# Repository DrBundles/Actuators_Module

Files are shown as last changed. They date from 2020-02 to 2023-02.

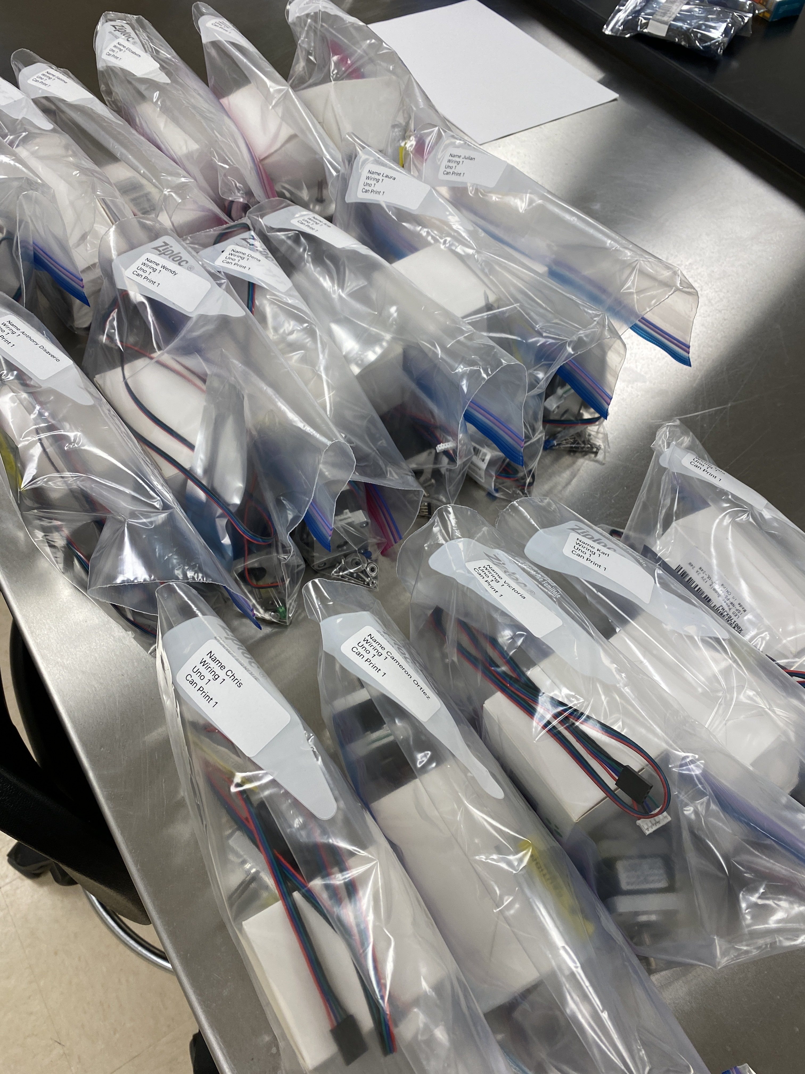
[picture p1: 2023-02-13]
Parts/Parts_Pickup_1.JPG

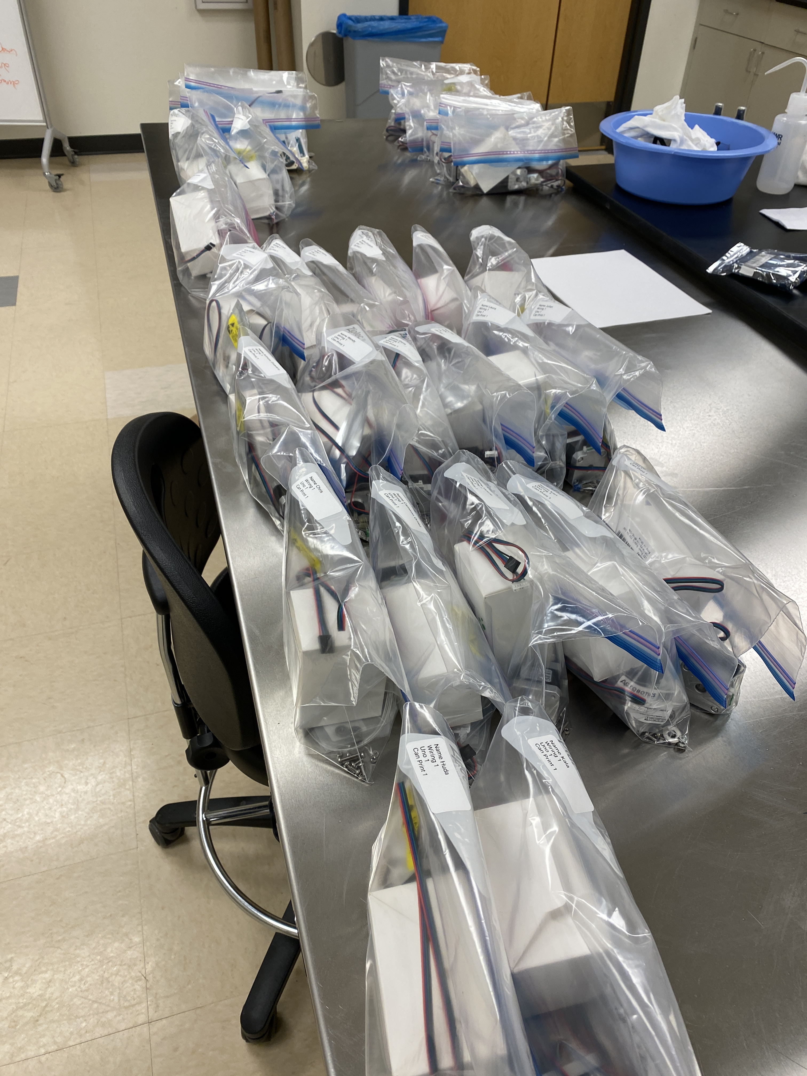
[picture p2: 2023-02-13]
Parts/Parts_Pickup_2.JPG

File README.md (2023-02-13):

# Actuators_Module

# Video Links
- [Materials Part 1](https://ucdenver.hosted.panopto.com/Panopto/Pages/Viewer.aspx?id=055986f1-c3ec-4268-8f4e-aeb30160cd68)
- [Code Day 1 Part 1](https://ucdenver.hosted.panopto.com/Panopto/Pages/Viewer.aspx?id=c7519612-6c13-432e-b2ea-aeb30160e118) 
- [Code Day 1 Part 2](https://ucdenver.hosted.panopto.com/Panopto/Pages/Viewer.aspx?id=c81cfcb9-6042-4e62-9a67-aeb30160f008)
- [Code Day 2 Part 1](https://ucdenver.hosted.panopto.com/Panopto/Pages/Viewer.aspx?id=9c95f3c9-c75f-416a-9927-aeb30160e0f4)
- [Code Day 2 Part 2](https://ucdenver.hosted.panopto.com/Panopto/Pages/Viewer.aspx?id=abec7e0b-8e1e-48be-8ef7-aeb301610b54)
- [Code Day 2 Part 3](https://ucdenver.hosted.panopto.com/Panopto/Pages/Viewer.aspx?id=a6deae2b-6028-43d2-8763-aeb30160e47a)
- [Code Day 3 Part 1](https://ucdenver.hosted.panopto.com/Panopto/Pages/Viewer.aspx?id=0ca2a75e-c111-4d63-9ddc-aeb30160e49d)

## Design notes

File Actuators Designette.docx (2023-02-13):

# Actuators Designette

Lecture Notes:

- Students will be given the User Story and User Needs.
- Design Inputs will be filled in together in-class as a discussion.
- Students will be given one design output and one corresponding verification test.
- Students will generate their own Design Outputs and corresponding verification tests that match up with the given Design Inputs.
- Validation tests will be provided but not completed as part of this experiment.
- Measuring of Rotational Speed will be extra credit if the students develop a method to do this in lab. Otherwise, it will need to be detailed how this would be done in practice within the Design Process documentation.

# User Story

Would you help me to design a new motor to drive my machine? My old motor died and I need to replace it. I have to turn a ¼” shaft at precisely 122RPM for 12.234 seconds. This process must operate in concert with my other equipment so I need it to be electronically controlled. Also, the current machine does not let us know what the actual RPM is. It would be really nice to know what the RPM is so we can track it as part of our QMS. We don’t need to automatically log this information though, we can just read it off of a screen. Thanks for the help!

Torque!

# User Needs

ID | Title | Description
UN-1 | Rotational Output | The user needs to rotate a ¼” shaft.
UN-2 | Rotation RPM | The user needs to rotate a shaft at 122RM
UN-3 | Rotation Controls | The user needs to control the shaft motion automatically, not using a manual switch.
UN-4 | Rotation Duration | The user needs to precisely control the duration of rotation to 12.234 seconds.
UN-5 | Rotation Measuring | The user needs a method to monitor shaft rotational speed for QMS.

## Design Inputs

ID | Link | Title | Description
DI-1 | UN-1 | Connection | The device shall mechanically couple to a ¼ inch input shaft.
DI-2 | UN-1 | Motion | The device shall rotate the input shaft detailed in DI-1.
DI-3 | UN-2 | RPM Speed | The device shall rotate the input shaft detailed in DI-2 at 122 RPM ±1 RPM.
DI-4 | UN-3 | Controls | The device shall be controlled through automatic actuation that interfaces with the existing electronic system.
DI-5 | UN-4 | Duration | The device shall rotate the output shaft detailed in DI-1 at the rate detailed in DI-3 for 12.234 ± .001 seconds.
DI-6 | UN-5 | RPM Measure | The device shall provide a visual indication of the RPM speed detailed in DI-3.

## Design Outputs

ID | Link | Title | Description
DO-1 | DI-1 | Shaft Coupling | The device shall mechanically mate with the user’s ¼” input shaft through a rigid set-screw type coupling.
DO-2 | DI-2 DI-3 | Motor | The device will use a DC brushed gearhead motor coupled to a custom gearbox to achieve the 122 RPM rotational motion.
DO-3 | DI-2 | Housing | The motor and gearbox shall be affixed to a housing.
DO-4 | DI-1 DI-2 | Housing Mount | The motor housing will be affixed to the existing machine frame using the existing threaded mounting holes utilized by the previous motor housing.
DO-5 | DI-2 DI-4 | Motor Power | The device motor shall use the same 12V DC supply as the previous electric motor (3A max load).
DO-6 | DI-4 DI-5 DI-6 | Controls Microcontroller | The device will use an Arduino microcontroller to control motor state (on/off), runtime duration, and RPM measurement and indication.
DO-7 | DI-4 DI-5 | Motor Controls | The electric motor will be switched using a power MOSFET rated for the appropriate load based on the chosen electronic components.
DO-8 | DI-6 | RPM Measurement | The output shaft rotational speed will be measured using a photodiode / laser encoder that is monitored by the Arduino firmware.
DO-9 | DI-6 | RPM Indication | RPM values will be indicated to the user through a USB / serial connection. Values will be shown in the Arduino Serial Plotter running on a computer monitor.

## Verification

ID | Link | Title | Description | Test Protocol
VE-1 | DI-1 | Connection to Shaft | Test that the device mechanically connects to a ¼” shaft in a manner that allows for rotary motion without slippage or misalignment. | PV-1
VE-2 | DI-1 | Mounting | Test that the motor housing bolt pattern matches the bolt pattern dimensions on the existing equipment. | PV-2
VE-3 | DI-2 | Rotation | Test that the gearbox and shaft allow for unrestricted rotational motion by removing the gearhead motor and manually turning the input drive gear. | PV-3
VE-4 | DI-3 | RPM | Test that output shaft rotates at 122 RPM ±1 RPM. | PV-4
VE-5 | DI-4 | Controls | Test that the Arduino can automatically change the motor state (on/off). | PV-5
VE-6 | DI-5 | Duration | Verify that the device drive motor remains energized and in motion for 12.234 ± .001 seconds | PV-6
VE-7 | DI-6 | RPM Measure | Verify that the RPM value as measured by the encoder and Arduino matches the value as measured using the independent technique outlined in VE-4. | PV-7
VE-8 | DI-6 | RPM Indication | Verify that the RPM value measured in VE-7 matches the value indicated within the user interface. | PV-8

## Validation

ID | Link | Title | Description | Test Protocol
VL-1 | UN-1 | Mounting | Test that the motor, gearbox and housing successfully mounts to the existing equipment as detailed in DO-4. | PL-1
VL-2 | UN-1 | Connection to Shaft | Test that the device mechanically connects to the existing ¼” input shaft in a manner that allows for rotary motion without slippage or misalignment. This test shall be conducted with the motor housing mounted to the existing frame. | PL-2
VL-3 | UN-2 | Rotation | Test that the gearbox and shaft allow for unrestricted rotational motion by removing the gearhead motor and manually turning the input drive gear while the housing and input shaft is mounted to existing equipment. | PL-3
VL-4 | UN-2 | Rotation | Test that the energized motor can rotate the input drive shaft of existing equipment. | PL-3
VL-5 | UN-2 | RPM | Test that output shaft rotates at 122 RPM ±1 RPM while connected to existing equipment. | PL-3
VL-6 | UN-3 | Controls | Test that the Arduino can automatically change the motor state (on/off) when controlled by input signal from existing equipment | PL-4
VL-7 | UN-4 | Duration | Test that the device drive motor remains energized and in motion for 12.234 ± .001 seconds while connected to existing equipment. | PL-5
VL-8 | UN-5 | RPM Measure | Test that the RPM value as measured by the encoder and Arduino is displayed and can be read by the user. | PL-6
VL-9 | UN-1 UN-2 UN-3 UN-4 | User Interface | Test that the user can properly use new device when operating existing equipment. | PL-7

## Traceability Matrix

Build a traceability matrix that has some values omitted. Students must fill in the omitted values.

NOTE: Add titles to the Trace matrix below

User Need | Design Input | Design Output | Verification | Validation
UN-1 | DI-1 | DO-1,4 | VE-1 | VL-2
| | | VE-2 | VL-1
| DI-2 | DO-2,3,4,5 | VE-3 | VL-9
UN-2 | DI-3 | DO-2 | VE-4 | VL-3
| | | | VL-4
| | | | VL-9
UN-3 | DI-4 | DO-5,6,7 | VE-5 | VL-6
| | | | VL-9
UN-4 | DI-5 | DO-6,7 | VE-6 | VL-7
| | | | VL-9
UN-5 | DI-6 | DO-6,8,9 | VE-7 | VL-8
| | DO-6,8,9 | VE-8

## Testing Protocols

One sample test protocol, students must generate several more test protocols.

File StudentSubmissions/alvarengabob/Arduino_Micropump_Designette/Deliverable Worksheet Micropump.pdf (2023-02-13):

Intro. to Biodesign
BIOE 3090 | Design Controls Worksheet

## Micropump Module

### Design Controls Worksheet – 50 Pts

## ID: DCW-1

Due Date: 2/13/2020 11:59 PM, Canvas Upload

Date Written – 04/02/2020
Date Revised – 04/04/2020
Author: Alyssa Salazar, Bob Alvarenga, Gage Murray, Luis Rodriguez, Mikala Mueller

## Improvement of Existing Design User Needs

User Needs Matrix
ID | Description
UN-1 | Improved UX / UI to allow for operator control.
UN-2 | Improve Solidworks files to include assembly, hardware, configurations, and drawings.
UN-3 | Eliminate warping of printhead resulting in motor temperature when located in an incubator.
UN-4 | A method to stop or detach pump heads individually when part of a multi-pump design.
UN-5 | Eliminate breadboard or prototype parts in the circuit.

## Design Inputs

Requirements Matrix
Requirement ID | Requirement
DI-1 | The device shall have a user interface to set the pump flow rate.
DI-2 | The device shall be easier to assemble.
DI-3 | The design shall be less than 64 cm² .
DI-4 | The design shall allow for detachment of individual pumps.
DI-5 | The device shall have a printed circuit board (PCB).

## Design Outputs

Design Outputs Matrix
Requirement ID | Requirement
DO-1 | The device shall operate with a variable flow rate.
DO-2 | The device shall be assembled using simple instructions.
DO-3 | The design board shall be printed for the optimal design.
DO-4 | The design shall operate with a detachment of individual pumps.
DO-5 | The electrical components shall be soldered to the printed board for compact design

## Design Verification

Verification Matrix – Write at least 5 Verification tests that
Requirement ID | Description | Expected Value | Measured Value | Pass/Fail
DI-1 | UI is changeable to set the flow rate. | Yes | Yes | Pass
DI-2 | People without experience in circuit assembly are able to build the device following instructions. | Yes | Yes | Pass
DI-3 | Area is less than 24 cm² . | 7 cm² | | Pass
DI-4 | Device continues to operate after detachment of individual pumps. | Yes | Yes | Pass
DI-5 | The device has a PCB. | Yes | Yes | Pass

## Design Validation

Validation Matrix
User Need ID | Description | Expected Value | Measured Value | Pass/Fail
UN-2 | Device assembly is easier | Yes | Yes | Pass
UN-1 | UI improved | Yes | Yes | Pass
UN-3 | No warping of the printhead | Yes | Yes | Pass
UN-4 | Pumpheads able to be removed individually | Yes | Yes | Pass
UN-4 | Pumpheads able to be stopped | Yes | Yes | Pass
UN-5 | Breadboard eliminated | Yes | Yes | Pass

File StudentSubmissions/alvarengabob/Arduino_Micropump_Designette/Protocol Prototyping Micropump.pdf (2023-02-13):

Intro. to Biodesign
BIOE 3090 | Micropump – Prototyping Protocol

## Micropump Module

### Prototyping Protocol – 10 Pts

## ID: PP-1

Due Date: 2/13/2020 11:59 PM, Canvas Upload

Date Written – 04/02/2020
Date Revised – 04/04/2020
Author:Bob Alvarenga, Alyssa Salazar, Mikala Mueller, Luis Rodriguez, Gage Murray Protocol Description – (Prototyping Protocol)
This protocol outlines the steps necessary to create and design a PCB board using Eagle software to make the pump device more compact and easier to assemble. The device components were first tested on a breadboard to confirm the pump worked before designing in Eagle software. In Eagle software, the parts for the stepper motor driver, wall power interface, Arduino Uno, push button, LED light, and other components were placed into the schematic. Once the schematic had all components, lines representing the wire tracings were placed to corresponding locations to match the circuit. This was done as neatly as possible to allow for minimal confusion. A breadboard file was then generated and traces were laid in accordance to PCB manufacturer recommendations (thickness, angle). Once the schematic and breadboard file is completed, a corresponding Gerber file can then be generated in order to send to the manufacturer to create a PCB board that fits over the Arduino, an Arduino shield.
After the PCB board is printed it must have the circuit electronic components soldered onto the correct locations to allow the device to fit properly onto the Arduino, following the locations outlined in the schematic. Once these are soldered, the Arduino can be connected to the computer to have the control code uploaded to it, if not already uploaded, and test the motor and pump. If everything works accordingly, the device should be easier to assemble in the field and be able to be stored in smaller locations.

Tools and Equipment
ID | Tool | Name / # if applicable | Location | Purpose
PT1 | Computer | Mac Book | N/A | Design and create parts; Upload code to Arduino and change the pump flow rate
PT2 | Circuit Software | Eagle | N/A | PCB board-specific software
PT3 | Soldering Kit | Elenco Deluxe | Design Lab | To connect parts of the circuit
PT4 | Arduino Uno | Arduino Uno | Design Lab | To run the circuit
PT5 | Arduino IDE Software | Arduino Software | N/A | To program the code for the circuit

Materials
ID | Material | Purpose
PM1 | Fiberglass | Create PCB board
PM2 | Epoxy Resin | Create PCB board
PM3 | Copper foil/plate | Create PCB board
PM4 | Wires | Circuit Assembly
PM5 | Resistors | Circuit Assembly
PM6 | Capacitor | Circuit Assembly
PM7 | LED | Circuit Assembly
PM8 | Button | Circuit Assembly
PM9 | Stepper Motor Driver | Circuit Assembly
PM10 | Stepper Motor | Pump Assembly
PM11 | Pump Housing | Pump Assembly

PM12 | Pump Rotor | Pump Assembly
PM13 | Bearings | Pump Assembly
PM14 | Screws | Pump Assembly
PM15 | Nuts | Pump Assembly
PM16 | Washers | Pump Assembly
PM17 | Tubing | Pump Assembly

Computer Files
ID | FileName / Link | Purpose | Location
CF1 | Pump_Disignette_PCB _SCH_BRD_Files.zip | PCB file | Google Drive
CF2 | Pump_Disignette_PCB _Gerber_Files.zip | PCB file | Google Drive
CF3 | PCB_Schematic.png | Circuit Schematic | Google Drive
CF4 | PCB_Breadboard.png | Circuit Schematic | Google Drive

Schematics:

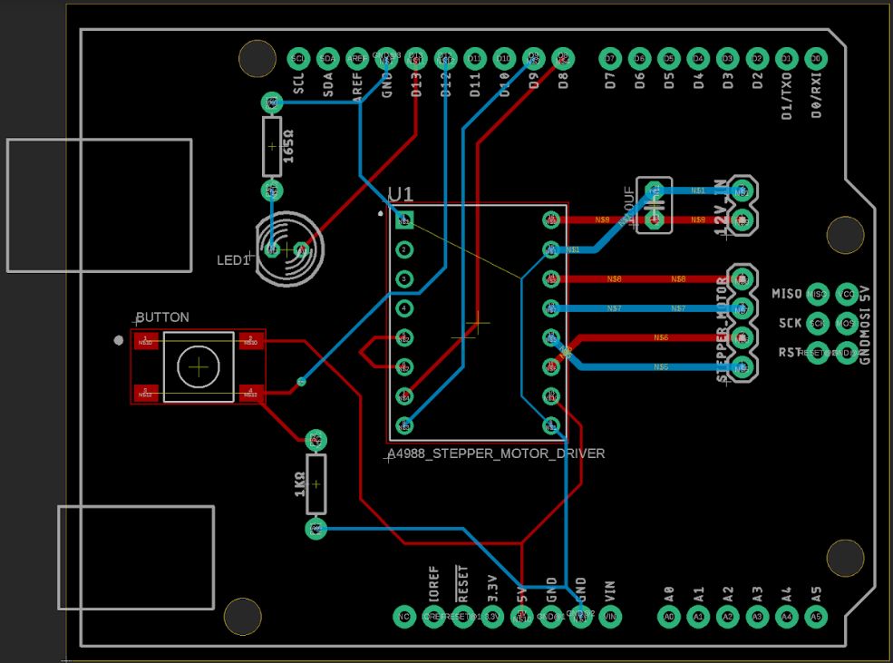
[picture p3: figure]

Figure 1. Schematic of PCB Breadboard. Schematic detailing the components of the breadboard and how each component is wired for pump functionality.

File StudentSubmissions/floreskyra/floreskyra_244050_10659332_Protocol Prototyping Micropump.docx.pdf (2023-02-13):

Intro. to Biodesign
BIOE 3090 | Micropump – Prototyping Protocol

## Micropumps

### Prototyping Protocol – 10 Pts

## ID: PP-1

Due Date: 4/6/2020 11:59 PM, Canvas Up

Date Written – 4/4/2020
Date Revised – 4/6/2020
Author: Kyra Flores, Ana Meza, Uyen Nguyen and Jonathan Tullos
Protocol Description – (Shaft Coupling)
This is the prototyping protocol used to create a shaft coupler that allows multiple peristaltic pump heads to run on a single motor. The shaft couple will allow for a longer shaft to be fitted to the motor, which would then allow for multiple pumps to fit on the shaft. The coupler can be milled on a drill press and all materials are available at most home improvement stores.
Tools and Equipment
ID | Tool | Name / # if applicable | Location | Purpose
PT1 | CAD program | Solidworks | Computer file | Design a prototype for the micropump and it’s parts if necessary
PT2 | Drill press | Stark 11 in. 6.6 Amp 120-Volt, 16-Speed Stationary Drill Press Floor Stand with Laser Light (https://www.homedepot.com/p/Stark-11-in-6-6-Amp-120-Volt-16-Speed-Stationary-Drill-Press-Floor-Stand-with-Laser-Light-53500-H/312129488) Model# 53500-H | Home Depot | Drill holes
PT3 | 7 mm steel thread taps | Drill America M7 x 0.5-High Speed Steel Hand Plug Tap (1-Piece) (https://www.homedepot.com/p/Drill-America-M7-x-0-5-High-Speed-Steel-Hand-Plug-Tap-1-Piece-DWTSMT7X-5/305700512) | Home Depot | Tap threads for set screws

| | Model# DWTSMT7X.5
PT4 | Vice | BESSEY 6 in. Heavy-Duty Bench Vise with Swivel Base (https://www.homedepot.com/p/BESSEY-6-in-Heavy-Duty-Bench-Vise-with-Swivel-Base-BV-HD60/205023093) Model# BV-HD60 | Home Depot | Holds the material steady to allows holes to be drilled
PT5 | 5mm Drill Bit | Drill America 5.00mm High Speed Steel Killer Force Drill Bit (12-Pieces) (https://www.homedepot.com/p/Drill-America-5-00mm-High-Speed-Steel-Killer-Force-Drill-Bit-12-Pieces-KFDMM5-00P12/304056739) Model# KFDMM5.00P1 2 | Home Depot | Bore main shaft holes
PT6 | 7mm Drill Bit | 7.00mm High Speed Steel Killer Force Drill Bit (12-Pieces) (https://www.homedepot.com/p/7-00mm-High-Speed-Steel-Killer-Force-Drill-Bit-12-Pieces-KFDMM7-00P12/304056728) Model# KFDMM7.00P1 2 | Home Depot | Bore set screw holes
PT7 | Hack Saw | Stanley 12 in. High-Tension Hack Saw with 10 in. Mini Hack Saw (https://www.homedepot.com/p/Stanley-12-in-High-Tension-Hack-Saw-with-10-in-Mini-Hack-Saw-20-036M/100496136) Model# 20-036M | Home Depot | Cut material to appropriate length

Materials
ID | Material | Purpose
PM1 | 20 mm steel bar | Shaft coupler body
PM2 | M7 set screws x 8 | Locks shafts into the coupler

Computer Files
ID | FileName / Link | Purpose | Location
CF1 | Shaft Coupler.SLDPRT | Design coupler | Google Drive (https://drive.google.com/open?id=1JlLHCzmQTze8ZmWeprAXWGa-_fWYLr53)

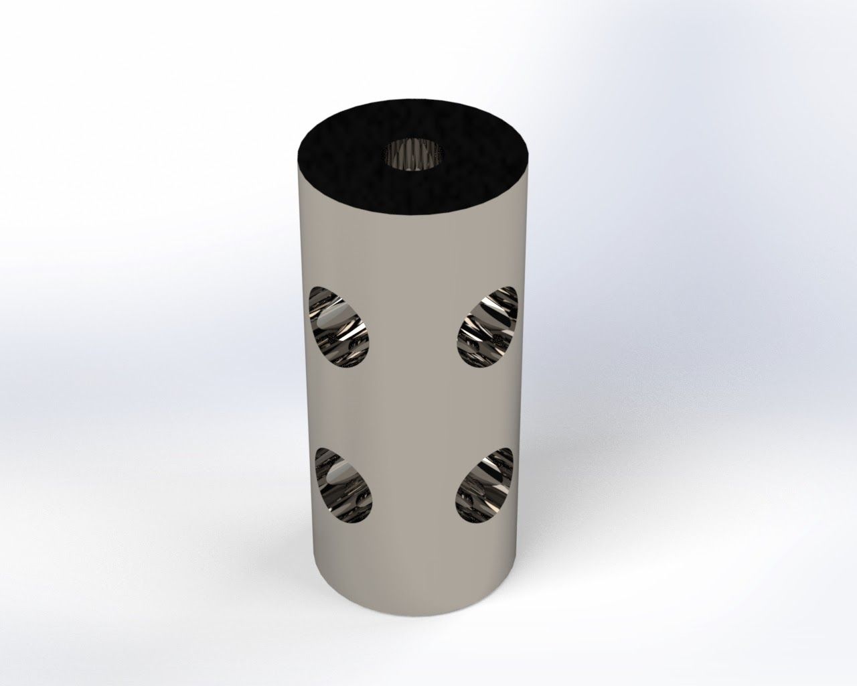
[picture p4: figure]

Figure 1. Render of the shaft coupler design.

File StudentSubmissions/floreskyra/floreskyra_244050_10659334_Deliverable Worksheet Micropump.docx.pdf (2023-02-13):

Intro. to Biodesign
BIOE 3090 | Design Controls Worksheet
Micropump | ID: DCW-1

Due Date: 4/6/2020 11:59 PM, Canvas Upload

Date Written – 4/4/2020
Date Revised – 4/6/2020
Author: Kyra Flores, Ana Meza, Uyen Nguyen, (https://ucdenver.instructure.com/courses/426016/users/217639) and Jonathan Tullos (https://ucdenver.instructure.com/courses/426016/users/223968)

## Improvement on Existing Design

## User Needs

User Needs Matrix

ID | Description
UN-1 | Improved UX / UI to allow for operator control.
UN-2 | Improve Solidworks files to include assembly, hardware, configurations, and drawings.
UN-3 | Eliminate warping of the printhead resulting in motor temperature when located in the incubator.
UN-4 | A method to stop or detach pump heads individually when part of a multi-pump design.
UN-5 | Eliminate breadboard or prototype parts in the circuit.

## Design Inputs

Requirements Matrix
Requirement ID | Requirement
DI-1 | The User Interface shall allow the user to set a pump flow rate.
DI-2 | The design files shall include assembly, hardware, configurations, and drawings.
DI-3 | The design shall be resistant to warping due to high temperatures.
DI-4 | The design shall allow individual pump heads to be detached or stop when it is a part of a multi-pump.
DI-5 | The design shall eliminate the use of breadboard or prototype parts in the circuit.

## Design Outputs

Design Outputs Matrix
Requirement ID | Requirement
DO-1 | The motor turns at a different calculated rate through inputting flow rate and tubing diameter from users
DO-2 | The design files include assembly, hardware, configurations, and drawings.
DO-3 | The pump housing does not change shape at 39 oC.
DO-4 | Various micropumps rotate with one motor.
DO-5 | The design will include a pcb.

Design Verification: The evaluation of whether or not a product, service, or

system complies with a regulation, requirement, specification, or imposed condition. It is often an internal process.
Verification Matrix – Write at least 5 Verification tests that
Requirement ID | Description | Expected Value | Measured Value | Pass/Fail
DI-1 | The micropump flow can calculate stepper rate by taking in the user interface: tubing type and desired volumetric flow rate for speed control
DI-2 | Solidworks files are available and accessible | N/A | N/A
DI-3 | The design must be able to withstand warping at the incubator temperature of 39 degree Celsius | >= 39 degree Celsius | N/A
DI-4 | Varying number of pumps can be turned by a single motor at an acceptable rate. | 5 pumps | N/A
DI-5 | The micropump must be able to pump fluids without the need of breadboard or large prototype parts | | N/A

## Design Validation:

Validation Matrix
User Need ID | Description | Expected Value | Measured Value | Pass/Fail
UN-1 | The stepper speed is controlled by taking in tubing type and desired volumetric flow rate, code can be executed from any reasonable inputs. If no valid input is | Flow rate = 0.5 mL/ms | N/A

| received, the default speed will run. | Tubing diameter = 0.3 cm
UN-2 | Solidworks files are available and accessible. | N/A | N/A
UN-3 | Pump housing withstands warping at 39 oC | >= 39 degree Celsius | N/A
UN-4 | Multiple pumps can be turned using a single motor. Individual specific pumps can be stopped and/or replaced within the multi-pump. | 1-5 pumps | N/A
UN-5 | The micropump pumps fluids at the set speed and volume without the use of breadboard or prototype parts in the circuit. | Desired set speed | N/A

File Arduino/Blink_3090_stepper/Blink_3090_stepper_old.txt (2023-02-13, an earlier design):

/*
  Blink_3090_timed

  Turns an LED on for one second, then off for one second, repeatedly.

  Pin 13 – Digital out: LED

  created 25 Feburary 2020
  by Steve Lammers

  This example code is in the public domain.

  Source code adapted from - http://www.arduino.cc/en/Tutorial/Blink
*/

// >>>>>>>>>>> Pin Definitions >>>>>>>>>>>>>>>>>>
#define LED_PIN 13
#define PB_PIN 12
#define STEP_PIN 8
#define DIR_PIN 9 
// <<<<<<<<<<< Pin Definitions <<<<<<<<<<<<<<<<<<

// >>>>>>>>>>> Globals >>>>>>>>>>>>>>>>>>>>>>>>>>
bool ledState = false;
double lastTime = 0;                  // milliseconds, holds time value during main loop
unsigned long currentTime = 0;        // milliseconds 
unsigned long switchTime = 1000;      // milliseconds between blinking LED on and off
unsigned long pbLastDebounceTime = 0; // milliseconds time of last pb press
unsigned long pbDebounceDelay = 50;   // milliseconds delay for pusbbutton debounce
int stepperDelay;                     // milliseconds between stepper motor steps
// <<<<<<<<<<< Globals <<<<<<<<<<<<<<<<<<<<<<<<<<

// ******************* Setup *********************
// the setup function runs once when you press reset or power the board
void setup() {
  // start serial port at 9600 bps:
  Serial.begin(9600);
  while (!Serial) {
    ; // wait for serial port to connect. Needed for native USB port only
  }
  // initialize digital pins 
  pinMode(LED_PIN, OUTPUT);
  pinMode(PB_PIN, INPUT);
  // initialize timers for LED blinking
  lastTime = millis();
  currentTime = lastTime;
  stepper_forward();
} // end setup

// ******************* Main Loop ******************
void loop() {

  // pbLatch is a local variable, does not have global scope
  // so it needs to be passed to and from functions.
  // Boolean latch for controlling LED blink
  bool pbLatch = false; 
  
  // Poll state of the pushbutton, debounce if signal detected
  if (digitalRead(PB_PIN)){
    pbLatch = pb_debounce(pbLatch);
  }
 
  // Check if it is time to blink the LED
  // and switch state if enough time has elapsed
  blink_timer(millis(), pbLatch);
  
  // Run stepper motor if PB is latched on
  if(pbLatch){
    run_stepper();
  }

} // end loop

// >>>>>>>>>>> Sub Functions >>>>>>>>>>>>>>>>>>
//
//
// ****************** blink_led ***************
//   Blinks LED on and off
//   
//  Arguments
//  int ledPin - Digital pin controlling LED
//
void blink_led(int ledPin, bool ledOnOff){
  digitalWrite(ledPin, ledOnOff);   // turn the LED on (HIGH is the voltage level)
}
//
//
//
// ****************** blink_timer ***************
// Timing loop for LED blinking
//
void blink_timer(unsigned long currentTime, bool pbLatch){

  if ((currentTime - lastTime) >= switchTime) {
    lastTime = currentTime;
    // Switch LED state if bBlink was triggered by timing loop
    if (pbLatch) {
      ledState = !ledState;
      blink_led(LED_PIN, ledState);
    }
  }
}
//
//
//
// ****************** pb_debounce ***************
// Debounce pushbutton signal
// This code uses a small delay since it is only
//   run intermittently and the main loop is holding
//   for signal most of the time this delay should not
//   prove a problem here.
//
bool pb_debounce(bool latchValue){
  pbLastDebounceTime = millis();
  delay(pbDebounceDelay);
  if(digitalRead(PB_PIN)){
    latchValue = !latchValue;
  }
  return latchValue;
}
//
//
//
// ****************** stepper_forward ***************
// Stepper motor step controls
//
void stepper_forward(void){
  digitalWrite(DIR_PIN, HIGH);
}
//
//
//
// ****************** stepper_backward **************
// Stepper motor step controls
//
void stepper_backward(void){
  digitalWrite(DIR_PIN, LOW);
}
//
//
//
// ****************** run_stepper *******************
// Stepper motor step controls
//
void run_stepper(void){
  digitalWrite(STEP_PIN, HIGH);
  delay(stepperDelay);
  digitalWrite(STEP_PIN, LOW);
  delay(stepperDelay);
}
//
//
// <<<<<<<<<<<< Sub Functions <<<<<<<<<<<<<<<<<<

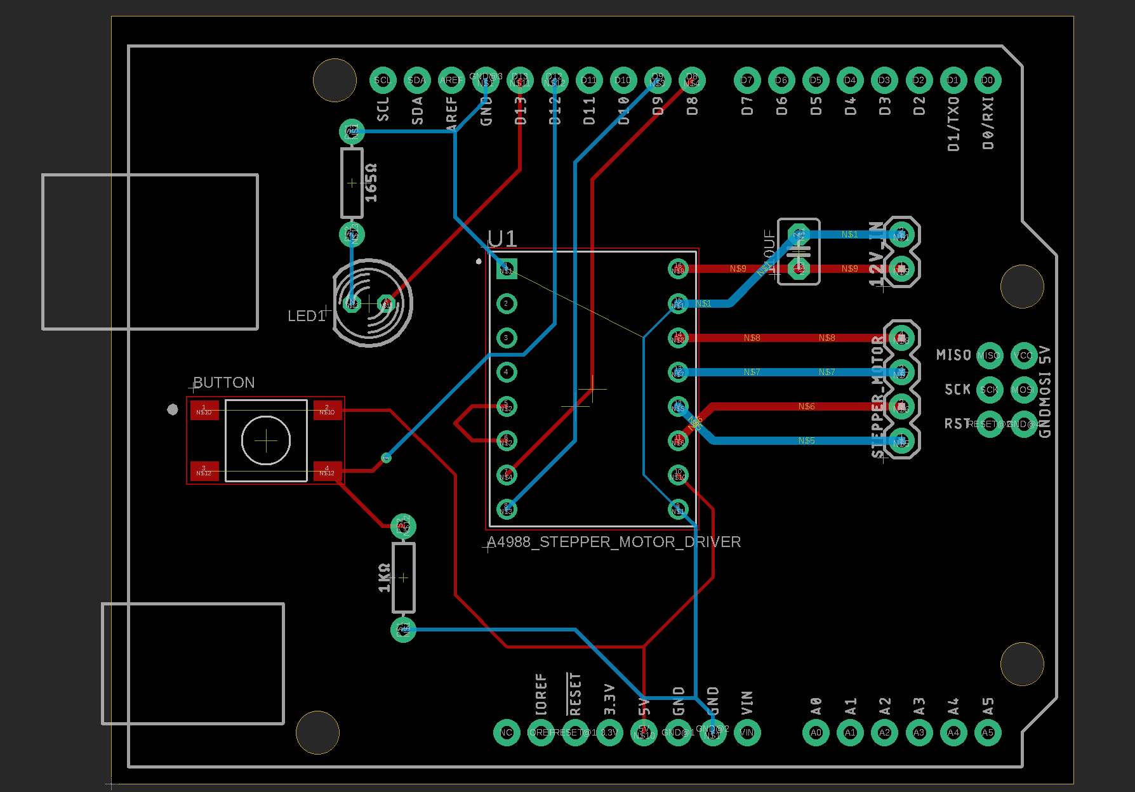
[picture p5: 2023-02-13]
StudentSubmissions/alvarengabob/Arduino_Micropump_Designette/PCB_Breadboard.png

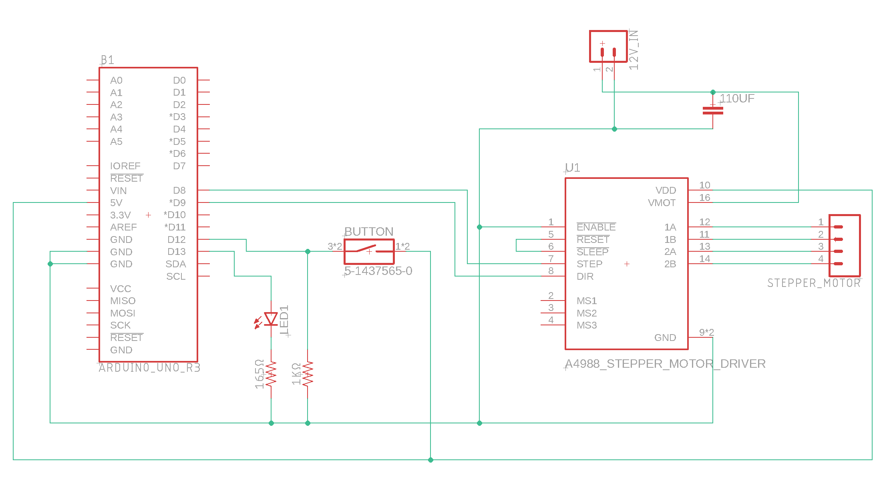
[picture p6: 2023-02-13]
StudentSubmissions/alvarengabob/Arduino_Micropump_Designette/PCB_Schematic.png

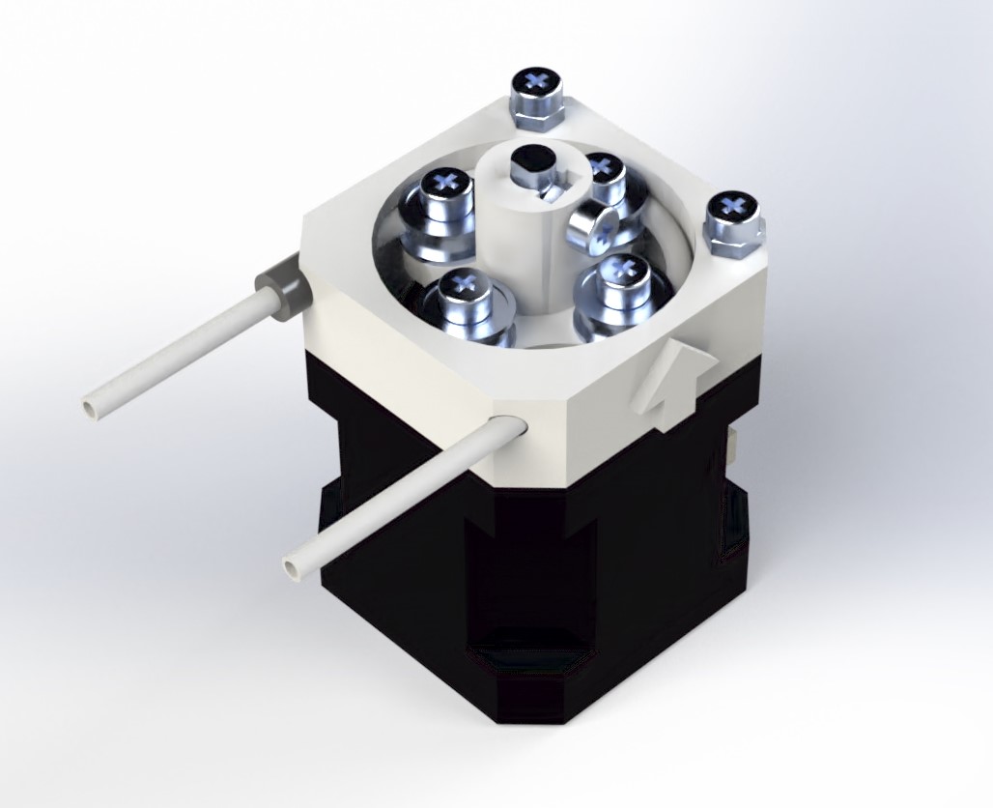
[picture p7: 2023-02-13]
StudentSubmissions/elkedwanimiray/Micropump SolidWork Files/Micropump/Right Side Render.jpg

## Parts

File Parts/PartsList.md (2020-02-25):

Parts List
=================

##Servo City Parts

-

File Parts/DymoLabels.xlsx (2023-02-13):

Type | part | Quantity
Screws | Pan Head M3 x 0.5, 8mm | 4
Screws | Pan Head M3 x 0.5, 6mm | 1
Screws | Pan Head M3 x 0.5, 16mm | 2
Nuts | Hex Nut M3 x 0.5 | 4
Nuts | Thin Hex Nut M3 x 0.5 | 1
Washers | Washer M3, 3.2 ID, 6 OD | 8
Washers | Washer 1/4" , 0.281" ID, 0.625" OD | 1
Ball Bearings | 1/8" ID x 3/8" OD Flang Ball Bearing | 4
Ball Bearings | Thin Square Nut M3 x 0.5 | 1
Stepper Parts | Stepper | 1
Stepper Parts | Stepper Driver | 1
Stepper Parts | Stepper Header Drivers - 1x4 0.1" long header | 1
Stepper Parts | pushbutton | 1
Misc Electrical Parts | LED | 2
Misc Electrical Parts | LED resistor - 165 Ohm | 1
Misc Electrical Parts | Pulldown resistors - 56k Ohm | 3
Misc Electrical Parts | Pulldown resistors - 10k Ohm | 2
Misc Electrical Parts | 100uF Cap | 1
Power | uC | Arduino | power supply | 1
Power | uC | Arduino | Arduino | 1
Power | uC | Arduino | wiring kits | N/A
Power | uC | Arduino | breadboard | N/A
Tubing | Tygon Tubing | 1
Tubing | tubing fittings | N/A
Tubing | Ziplock Bag Gallon | N/A
Plastic Parts | Pump Housing | 1
Plastic Parts | Pump Rotor | 1

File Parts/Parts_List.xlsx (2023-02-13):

Servo City
Part | Number | Link

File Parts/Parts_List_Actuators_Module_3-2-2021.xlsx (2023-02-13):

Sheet: Survey Answers
 | Breadboard | Wiring Kit | Uno | Can Print | Mail
Fatima | 1 | 1 | 1 | 1
Brenda | 1 | 1 | 1 | 1
Ashley | 1 | 1 | 0 | 0
Layla | 1 | 1 | 1 | 0
Anthony Nongiorno | 1 | 1 | 0 | 1
Anthony Disaverio | 1 | 1 | 1 | 1
Cameron | 1 | 1 | 0 | 0 |  | 2nd attempt?
Nasim | 1 | 1 | 1 | 0
Huda | 1 | 1 | 1 | 1
Leslie | 1 | 1 | 1 | 0
Derek | 1 | 1 | 0 | 0
Areeb | 1 | 1 | 0 | 0
Evgeni | 1 | 1 | 1 | 0
Elizabeth | 1 | 1 | 1 | 1
Abby | 1 | 1 | 1 | 1
Karl | 1 | 1 | 1 | 1
Carli | 1 | 1 | 1 | 1
Michael Millan | 1 | 0 | 1 | 1
Jacqueline | 1 | 1 | 1 | 0
Victoria | 1 | 1 | 1 | 1
Tala | 1 | 1 | 1 | 1
Martha | 1 | 1 | 1 | 0
Cameron Ortiez | 1 | 1 | 1 | 1
Chris | 1 | 1 | 1 | 1
Gabriela | 1 | 1 | 1 | 0
Juilan | 1 | 1 | 1 | 1
Laura | 1 | 1 | 1 | 1
Nestor | 1 | 1 | 1 | 1
Dena | 1 | 1 | 1 | 1
Aria | 1 | 1 | 1 | 1
Wendy | 1 | 1 | 1 | 1
Kristin | 1 | 1 | 0 | 1
Kala | 1 | 1 | 1 | 1
Num Submitted | 33
Num Students | 33
Sum Answers | 33 | 32 | 27 | 22
Parts Needed | 0 | 1 | 6 | 11

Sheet: Parts List Ea Student
 | Description | Vendor | Part Number | Quantity each student
Mechanical | Screws
 | Pan Head M3 x 0.5, 8mm | McMaster | 92000A118 | 4
 | Pan Head M3 x 0.5, 6mm | McMaster | 92000A116 | 1
 | Pan Head M3 x 0.5, 16mm | McMaster | 92000A126 | 2
 | Nuts
 | Hex Nut M3 x 0.5 | McMaster | 91828A211 | 4
 | Thin Hex Nut M3 x 0.5 | McMaster | 90710A030 | 1
 | Thin Square Nut M3 x 0.5 | McMaster | 97259A101 | 1
 | Washers
 | Washer M3, 3.2 ID, 6 OD | McMaster | 98689A112 | 8
 | Washer 1/4" , 0.281" ID, 0.625" OD | McMaster | 92141A029 | 1
 | Ball Bearings
 | 1/8" ID x 3/8" OD Flang Ball Bearing | Servo City | 535206 | 4
Electrical | Stepper Parts
 | Stepper | Amazon | B07QW21PXK | 1
 | Stepper Driver | Amazon | B01FFGAKK8 | 1
 | Stepper Header Drivers - 1x4 0.1" long header |  | S1241E-04-ND‎ (https://punchout.digikey.com/product-detail/en/PBC04SFDN/S1241E-04-ND/860021/?itemSeq=356242687) | 1
 | pushbutton | Amazon | B06XT3FLVM | 1
 | Misc Electrical Parts
 | LED | Amazon |  | 2
 | LED resistor - 165 Ohm | Digikey | MFR-25FBF52-165R‎ | 1
 | Pulldown resistors - 56k Ohm | Digikey | CF14JT56K0CT-ND‎ (https://punchout.digikey.com/product-detail/en/CF14JT56K0/CF14JT56K0CT-ND/1830393/?itemSeq=356240625) | 3
 | Pulldown resistors - 10k Ohm |  |  | 2
 | 100uF Cap | Digikey | P5152-ND‎ (https://punchout.digikey.com/product-detail/en/ECA-1EM101/P5152-ND/245011/?itemSeq=356241435) | 1
 | Power | uC | Arduino
 | power supply | Amazon | B01GD4ZQRS | 1
 | Arduino | Amazon |  | 1
 | wiring kits | N/A |  | N/A
 | breadboard | N/A |  | N/A
Other | Tygon Tubing | ~12in length |  | 1
 | tubing fittings | N/A |  | N/A
 | Ziplock Bag Gallon
Printed Parts | Pump Housing | Some Students can Print this themselves |  | 1
 | Pump Rotor | Some Students can Print this themselves |  | 1

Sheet: Dymo Labels
Type | part | Quantity
Screws | Pan Head M3 x 0.5, 8mm | 4
Screws | Pan Head M3 x 0.5, 6mm | 1
Screws | Pan Head M3 x 0.5, 16mm | 2
Nuts | Hex Nut M3 x 0.5 | 4
Nuts | Thin Hex Nut M3 x 0.5 | 1
Washers | Washer M3, 3.2 ID, 6 OD | 8
Washers | Washer 1/4" , 0.281" ID, 0.625" OD | 1
Ball Bearings | 1/8" ID x 3/8" OD Flang Ball Bearing | 4
Ball Bearings | Thin Square Nut M3 x 0.5 | 1
Stepper Parts | Stepper | 1
Stepper Parts | Stepper Driver | 1
Stepper Parts | Stepper Header Drivers - 1x4 0.1" long header | 1
Stepper Parts | pushbutton | 1
Misc Electrical Parts | LED | 2
Misc Electrical Parts | LED resistor - 165 Ohm | 1
Misc Electrical Parts | Pulldown resistors - 56k Ohm | 3
Misc Electrical Parts | Pulldown resistors - 10k Ohm | 2
Misc Electrical Parts | 100uF Cap | 1
Power | uC | Arduino | power supply | 1
Power | uC | Arduino | Arduino | 1
Power | uC | Arduino | wiring kits | N/A
Power | uC | Arduino | breadboard | N/A
Tubing | Tygon Tubing | 1
Tubing | tubing fittings | N/A
Tubing | Ziplock Bag Gallon | N/A
Plastic Parts | Pump Housing | 1
Plastic Parts | Pump Rotor | 1

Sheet: Parts Order List Final
 | Number of Students | 35 | 34 + 1
 | Description | Vendor | Part Number | Quantity each student | Cost Per Pkg | Pkg pcs | Pcs needed | # Pkgs Needed | Total Cost | Website
Mechanical | Pan Head M3 x 0.5, 8mm | McMaster | 92000A118 | 4 | 4.56 | 100 | 140 | 2 | 9.12
 | Thin Square Nut M3 x 0.5 | McMaster | 97259A101 | 1 | 8 | 100 | 35 | 1 | 8
 | Thin Hex Nut M3 x 0.5 | McMaster | 90710A030 | 1 | 6.86 | 100 | 35 | 1 | 6.86
 | Hex Nut M3 x 0.5 | McMaster | 91828A211 | 4 | 5.55 | 100 | 140 | 2 | 11.1
 | Pan Head M3 x 0.5, 6mm | McMaster | 92000A116 | 1 | 5.83 | 100 | 35 | 1 | 5.83
 | Washer M3, 3.2 ID, 6 OD | McMaster | 98689A112 | 8 | 2.71 | 100 | 280 | 3 | 8.13
 | Washer 1/4" , 0.281" ID, 0.625" OD | McMaster | 92141A029 | 1 | 3.47 | 100 | 35 | 1 | 3.47
 | Pan Head M3 x 0.5, 20mm | McMaster | 92000A128 | 2 | 6.87 | 100 | 70 | 1 | 6.87
 | Pan Head M3 x 0.5, 16mm | McMaster | 92000A126 | 2 | 6.29 | 100 | 70 | 1 | 6.29
 |  |  |  |  |  |  |  |  | 65.67
 | 1/8" ID x 3/8" OD Flang Ball Bearing | Servo City | 535206 | 4 | 3.79 | 2 | 62 | 31 | 117.49 | https://www.servocity.com/1-8-id-x-3-8-od-flanged-ball-bearing-2-pack/
 | FR2zz Flanged Bearing Sealed | Lily Bearing | FR2-ZZ | 4 | 1.5 | 1 | 140 | 140 | 210 | https://www.lily-bearing.com/ball-bearings/miniature-bearing/miniature-flanged-bearings/inch-miniature-flanged-bearings/fr2zz/
 |  | Other Bearing Co | FR2-ZZ | 4 | 2.62 | 1 | 140 | 140
 |  |  |  |  |  |  |  |  | 327.49
Electrical | Stepper | Amazon | B07QW21PXK | 1 | 39.97 | 5 | 35 | 7 | 279.79 | https://www.amazon.com/gp/product/B07QW21PXK/ref=ppx_yo_dt_b_asin_title_o00_s00?ie=UTF8&psc=1
 | pushbutton | Amazon | B06XT3FLVM | 1 | 6.99 | 10 | 35 | 4 | 27.96 | https://www.amazon.com/gp/product/B06XT3FLVM/ref=ppx_yo_dt_b_asin_title_o00_s00?ie=UTF8&psc=1
 | LED resistor - 165 Ohm | Digikey | MFR-25FBF52-165R‎ | 1 | 0.022 | 1 | 35 | 250 | 5.5
 | LED | Amazon |  | 2 | 14.99 | 450 | 70 | 1 | 14.99 | https://www.amazon.com/gp/product/B073QMYKDM/ref=ppx_yo_dt_b_asin_title_o00_s00?ie=UTF8&psc=1
 | PB pulldown resistor - 56k Ohm | Digikey | CF14JT56K0CT-ND‎ (https://punchout.digikey.com/product-detail/en/CF14JT56K0/CF14JT56K0CT-ND/1830393/?itemSeq=356240625) | 2 | 0.01 | 1 | 70 | 250 | 2.5
 | Stepper Driver | Amazon | B01FFGAKK8 | 1 | 9.5 | 5 | 35 | 6 | 57 | https://www.amazon.com/gp/product/B01FFGAKK8/ref=ppx_yo_dt_b_asin_title_o00_s00?ie=UTF8&psc=1
 | Stepper Header Drivers - 1x4 0.1" long header |  | S1241E-04-ND‎ (https://punchout.digikey.com/product-detail/en/PBC04SFDN/S1241E-04-ND/860021/?itemSeq=356242687) | 1 | 0.415 | 1 | 35 | 50 | 20.75
 | 100uF Cap | Digikey | P5152-ND‎ (https://punchout.digikey.com/product-detail/en/ECA-1EM101/P5152-ND/245011/?itemSeq=356241435) | 1 | 0.09 | 1 | 35 | 100 | 9
 | wiring kits | N/A
 | breadboard | N/A
 | power supply | Amazon | B01GD4ZQRS | 1 | 7.99 | 1 | 35 | 35 | 279.65 | https://www.amazon.com/gp/product/B01GD4ZQRS/ref=ppx_yo_dt_b_asin_title_o01_s00?ie=UTF8&psc=1
 | step pin pulldown - 56k Ohm | Digikey | CF14JT56K0CT-ND‎ (https://punchout.digikey.com/product-detail/en/CF14JT56K0/CF14JT56K0CT-ND/1830393/?itemSeq=356240625) | 1 | 0.01 | 1 | 35 | 0 | 0
 | Arduino | Amazon |  | 1 | 26 | 1 | 6 | 8 | 208 | https://www.amazon.com/gp/product/B008GRTSV6/ref=ppx_yo_dt_b_asin_title_o00_s00?ie=UTF8&psc=1
 |  |  |  |  |  |  |  |  | 597.39
Other | Tygon Tubing
 | tubing fittings
 | Ziplock Bags Gallon
Printed Parts | Pump Housing |  |  |  |  |  | 11
 | Pump Rotor |  |  |  |  |  | 11
 |  |  |  |  |  |  |  | total | 990.55
 |  |  | 2057-PH1-04-UA-ND‎ (https://punchout.digikey.com/product-detail/en/PH1-04-UA/2057-PH1-04-UA-ND/9829296/?itemSeq=356242569) |  |  |  |  | per student | 28.30142857

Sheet: Parts Order List
 | Number of Students | 35 | 34 + 1
 | Description | Vendor | Part Number | Quantity each student | Cost Per Pkg | Pkg pcs | Pcs needed | # Pkgs Needed | Total Cost | Website
Mechanical | Pan Head M3 x 0.5, 8mm | McMaster | 92000A118 | 4 | 4.56 | 100 | 140 | 2 | 9.12
 | Thin Square Nut M3 x 0.5 | McMaster | 97259A101 | 1 | 8 | 100 | 35 | 1 | 8
 | Thin Hex Nut M3 x 0.5 | McMaster | 90710A030 | 1 | 6.86 | 100 | 35 | 1 | 6.86
 | Hex Nut M3 x 0.5 | McMaster | 91828A211 | 4 | 5.55 | 100 | 140 | 2 | 11.1
 | Pan Head M3 x 0.5, 6mm | McMaster | 92000A116 | 1 | 5.83 | 100 | 35 | 1 | 5.83
 | Washer M3, 3.2 ID, 6 OD | McMaster | 98689A112 | 8 | 2.71 | 100 | 280 | 3 | 8.13
 | Washer 1/4" , 0.281" ID, 0.625" OD | McMaster | 92141A029 | 1 | 3.47 | 100 | 35 | 1 | 3.47
 | Pan Head M3 x 0.5, 20mm | McMaster | 92000A128 | 2 | 6.87 | 100 | 70 | 1 | 6.87
 | Pan Head M3 x 0.5, 16mm | McMaster | 92000A126 | 2 | 6.29 | 100 | 70 | 1 | 6.29
 |  |  |  |  |  |  |  |  | 65.67
 | 1/8" ID x 3/8" OD Flang Ball Bearing | Servo City | 535206 | 4 | 3.79 | 2 | 62 | 234.98 | https://www.servocity.com/1-8-id-x-3-8-od-flanged-ball-bearing-2-pack/
 | FR2zz Flanged Bearing Sealed | Lily Bearing | FR2-ZZ | 4 | 1.5 | 1 | 140 | 210 | https://www.lily-bearing.com/ball-bearings/miniature-bearing/miniature-flanged-bearings/inch-miniature-flanged-bearings/fr2zz/
 |  | Other Bearing Co | FR2-ZZ | 4 | 2.62 | 1 | 140 | 366.8
Electrical | Stepper | Amazon | B07QW21PXK |  |  |  |  |  | https://www.amazon.com/gp/product/B07QW21PXK/ref=ppx_yo_dt_b_asin_title_o00_s00?ie=UTF8&psc=1
 | pushbutton | Amazon | B06XT3FLVM |  |  |  |  |  | https://www.amazon.com/gp/product/B06XT3FLVM/ref=ppx_yo_dt_b_asin_title_o00_s00?ie=UTF8&psc=1
 | LED resistor - 165 Ohm
 | LED
 | PB pulldown resistor - 56k Ohm
 | Stepper Driver | Amazon | B01FFGAKK8 |  |  |  |  |  | https://www.amazon.com/gp/product/B01FFGAKK8/ref=ppx_yo_dt_b_asin_title_o00_s00?ie=UTF8&psc=1
 | Stepper Header Drivers - 1x4 0.1" long header
 | 100uF Cap
 | wiring kits
 | breadboard
 | power supply | Amazon | B01GD4ZQRS |  |  |  |  |  | https://www.amazon.com/gp/product/B01GD4ZQRS/ref=ppx_yo_dt_b_asin_title_o01_s00?ie=UTF8&psc=1
 | step pin pulldown - 56k Ohm
 | Arduino
Other | Tygon Tubing
 | tubing fittings
Printed Parts | Pump Housing
 | Pump Rotor

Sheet: Sheet1
 | Number of Students | 35 | 34 + 1
 | Vendor | Part Number | Quantity each student | Description |  | Cost Per Pkg | Pkg pcs | Shipping | Total Cost | Website
Mechanical | McMaster | 92000A118 | 4 | 18-8 Stainless | Pan Head M3 x 0.5, 8mm
 | McMaster | 97259A101 | 1 | Low-Str Steel | Thin Square Nut M3 x 0.5
 | McMaster | 90710A030 | 1 | 18-8 Stainless | Thin Hex Nut M3 x 0.5
 | McMaster | 91828A211 | 4 | 18-8 Stainless | Hex Nut M3 x 0.5
 | McMaster | 92000A116 | 1 | 18-8 Stainless | Pan Head M3 x 0.5, 6mm
 | McMaster | 98689A112 | 8 | 18-8 Stainless | Washer M3, 3.2 ID, 6 OD
 | McMaster | 92141A029 | 1 | 18-8 Stainless | Washer 1/4" , 0.281" ID, 0.625" OD
 | McMaster | 92000A128 | 2 | 18-8 Stainless | Pan Head M3 x 0.5, 20mm
 | McMaster | 92000A126 | 2 | 18-8 Stainless | Pan Head M3 x 0.5, 16mm
 | Servo City | 535206 |  | Stainless | 1/8" ID x 3/8" OD Flang Ball Bearing
 |  |  | 4 | FR2zz Flanged Bearing | FR2zz Flanged Bearing |  | 2.62 | 4 | 140 | 366.8
Electrical | Stepper
 | pushbutton
 | LED resistor | 165 Ohm
 | LED
 | PB pulldown resistor | 56k Ohm
 | Stepper Driver
 | Stepper Header Drivers | 1x4 0.1" long header
 | 100uF Cap
 | wiring kits
 | breadboard
 | power supply
 | step pin pulldown | 56k Ohm
 | Arduino
Other | Tygon Tubing
 | tubing fittings
Printed Parts | Pump Housing
 | Pump Rotor

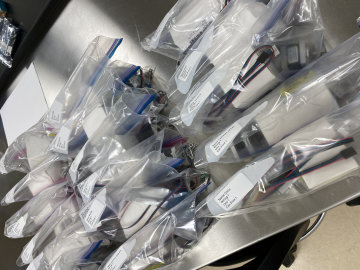
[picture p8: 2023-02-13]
Parts/Parts_Pickup_1_Sm.png

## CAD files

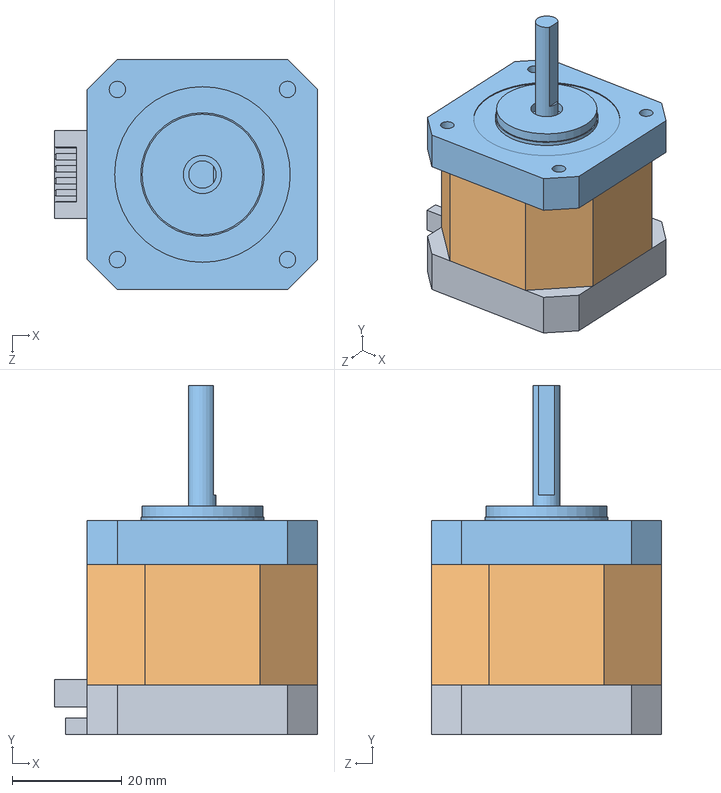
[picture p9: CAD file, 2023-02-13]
StudentSubmissions/elkedwanimiray/Micropump SolidWork Files/Micropump/Stepper Motor Assem.SLDASM
48.0 x 63.6 x 42.0 mm
Stepper Moter Base
Stepper Moter Middle
Stepper Moter Top

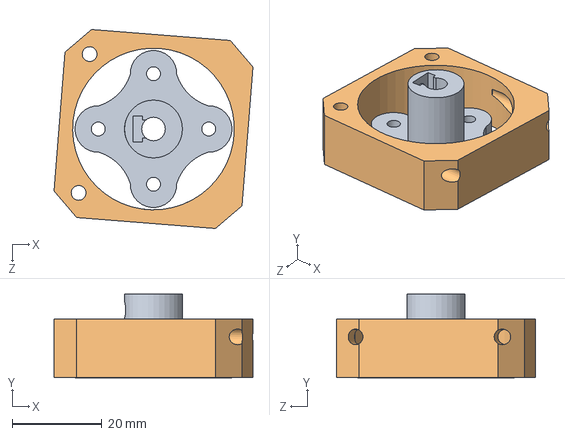
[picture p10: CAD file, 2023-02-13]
Pump/Pump_Assem.SLDASM
44.3 x 18.6 x 44.3 mm
Bearing_hub_spring_new2
Motor_enc_U

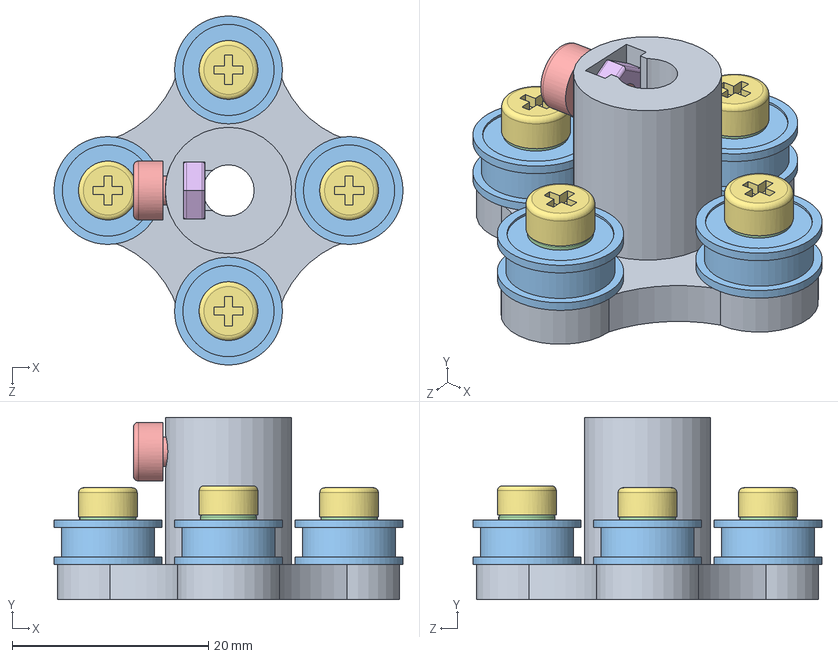
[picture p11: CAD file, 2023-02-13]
StudentSubmissions/elkedwanimiray/Micropump SolidWork Files/Micropump/Bearing Carrier Assem.SLDASM
35.6 x 18.6 x 35.6 mm
Bearing_hub_spring_new2
M3 Thin x 4
New bearing x 4
Washer Small x 4
Mini Screw
M3 Thicc
Small Screw x 4

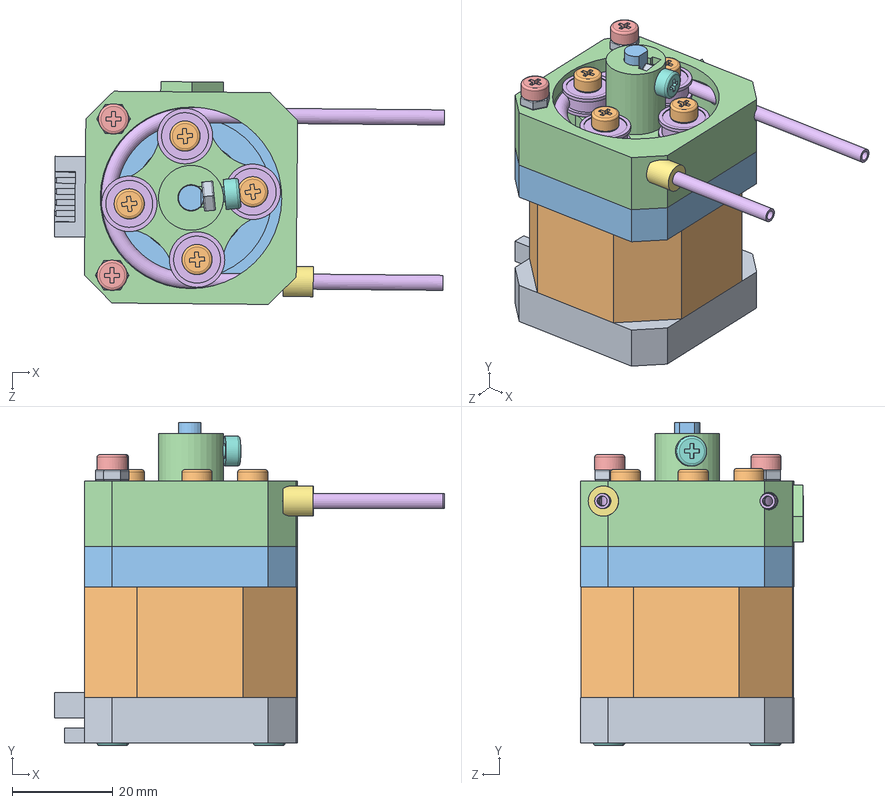
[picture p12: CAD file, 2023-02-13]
StudentSubmissions/elkedwanimiray/Micropump SolidWork Files/Micropump/Final Assembly.SLDASM
77.3 x 64.1 x 44.2 mm
Stepper Moter Base
Stepper Moter Middle
Stepper Moter Top
Bearing_hub_spring_new2
M3 Thin x 4
New bearing x 4
Washer Small x 4
Mini Screw x 5
M3 Thicc x 3
Small Screw x 4
Large Washer
Motor_enc_U
TopScrew x 2
Tubing
Shrink Wrap

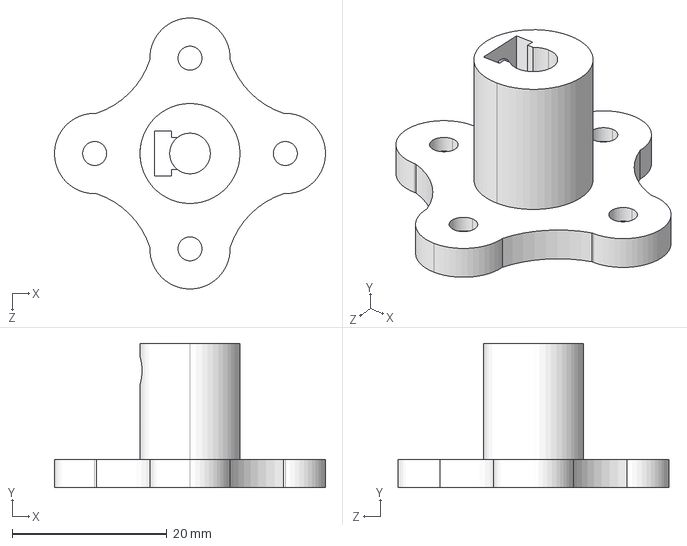
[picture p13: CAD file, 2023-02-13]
Pump/Bearing_hub_spring_new2.STEP
35.0 x 18.6 x 35.0 mm

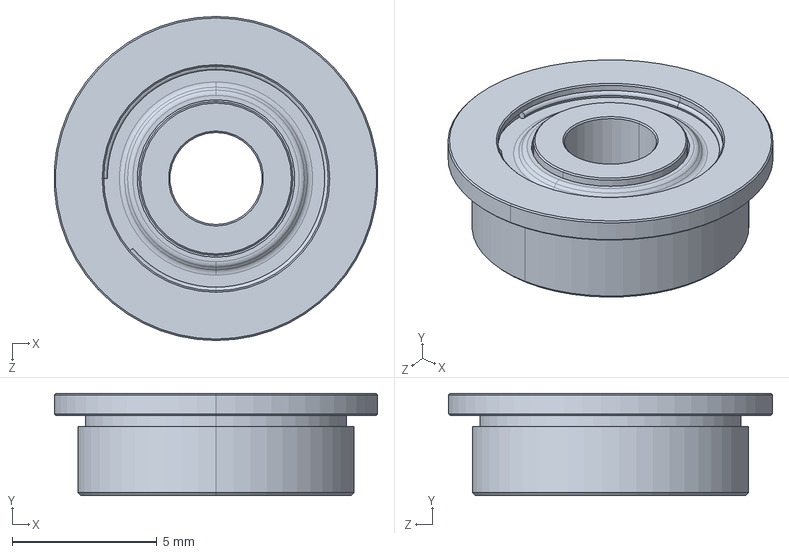
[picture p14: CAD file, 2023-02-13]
Pump/Bearing_535206.SLDPRT
11.2 x 3.53 x 11.2 mm

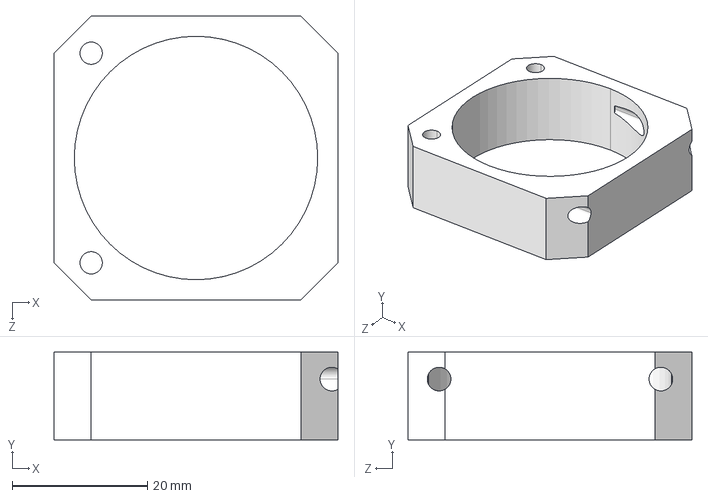
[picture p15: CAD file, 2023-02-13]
Pump/Motor_enc_U.STEP
42.0 x 13.0 x 42.0 mm

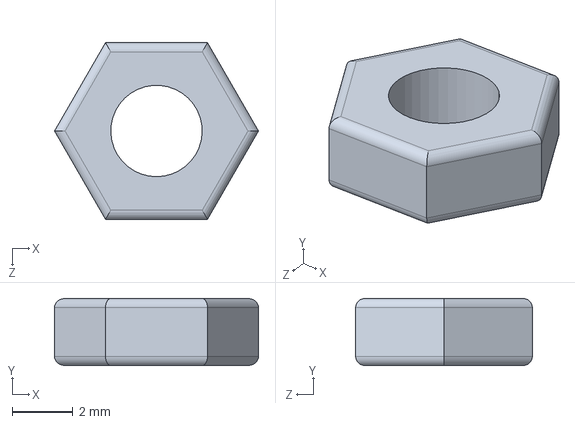
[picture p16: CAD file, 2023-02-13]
StudentSubmissions/elkedwanimiray/Micropump SolidWork Files/Micropump/M3 Thicc.SLDPRT
6.70 x 2.20 x 5.80 mm

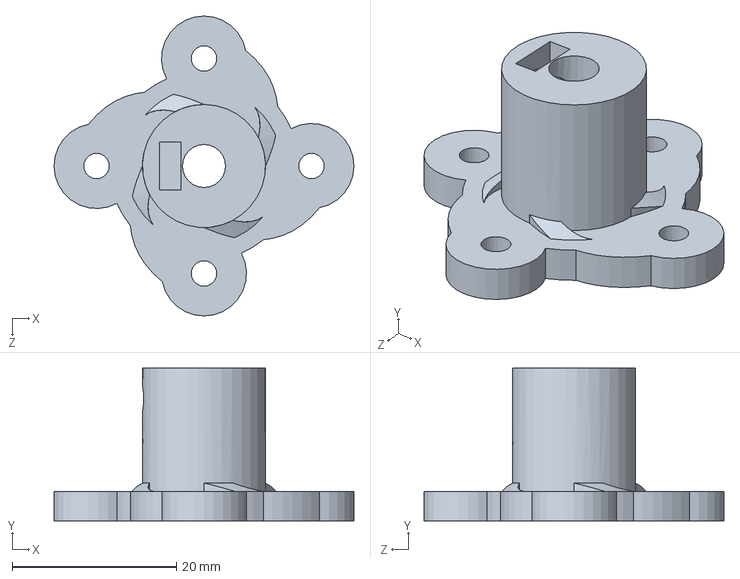
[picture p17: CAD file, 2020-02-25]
Pump/Bearing_hub_spring_new.SLDPRT
36.6 x 18.6 x 36.6 mm

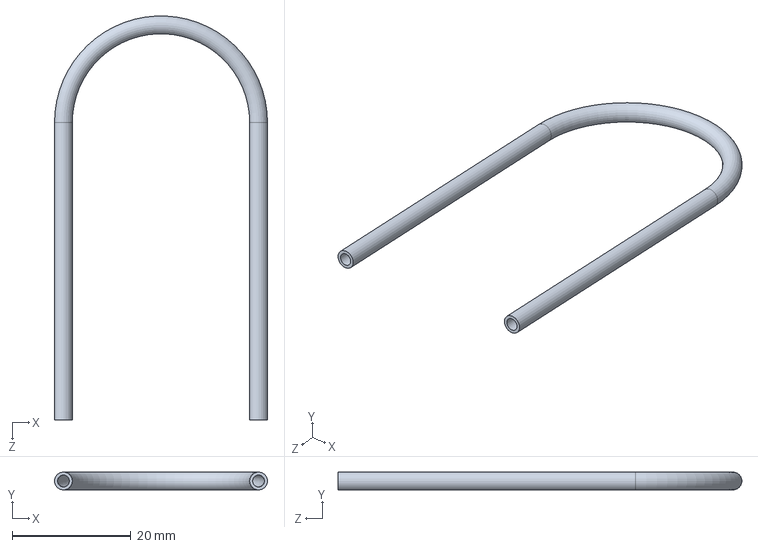
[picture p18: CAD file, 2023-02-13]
StudentSubmissions/elkedwanimiray/Micropump SolidWork Files/Micropump/Tubing.SLDPRT
35.8 x 3.00 x 67.9 mm

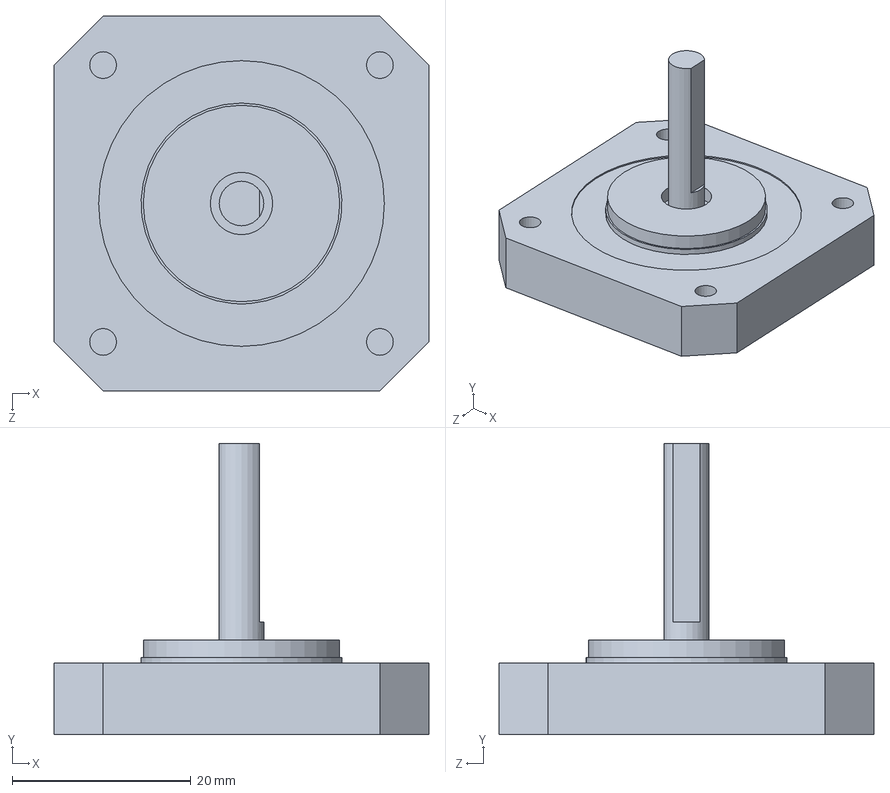
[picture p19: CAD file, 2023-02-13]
StudentSubmissions/elkedwanimiray/Micropump SolidWork Files/Micropump/Stepper Moter Top.SLDPRT
42.0 x 32.6 x 42.0 mm

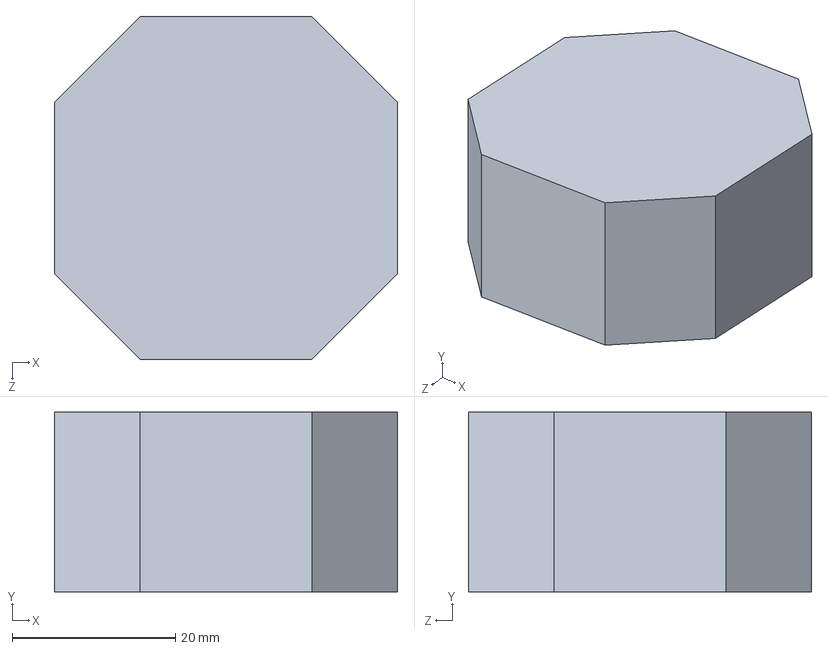
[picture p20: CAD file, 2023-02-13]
StudentSubmissions/elkedwanimiray/Micropump SolidWork Files/Micropump/Stepper Moter Middle.SLDPRT
42.0 x 22.0 x 42.0 mm

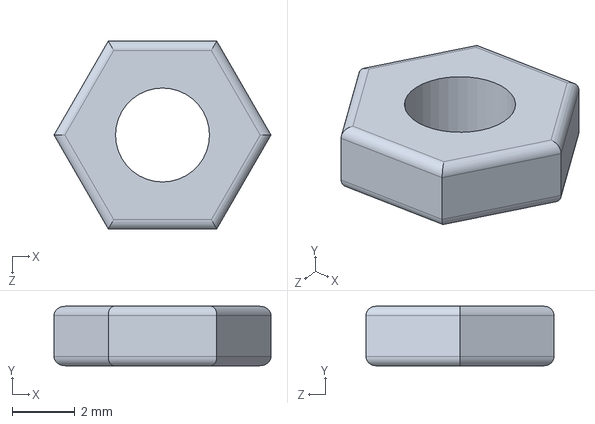
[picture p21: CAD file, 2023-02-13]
StudentSubmissions/elkedwanimiray/Micropump SolidWork Files/Micropump/M3 Thin.SLDPRT
6.93 x 1.90 x 6.00 mm

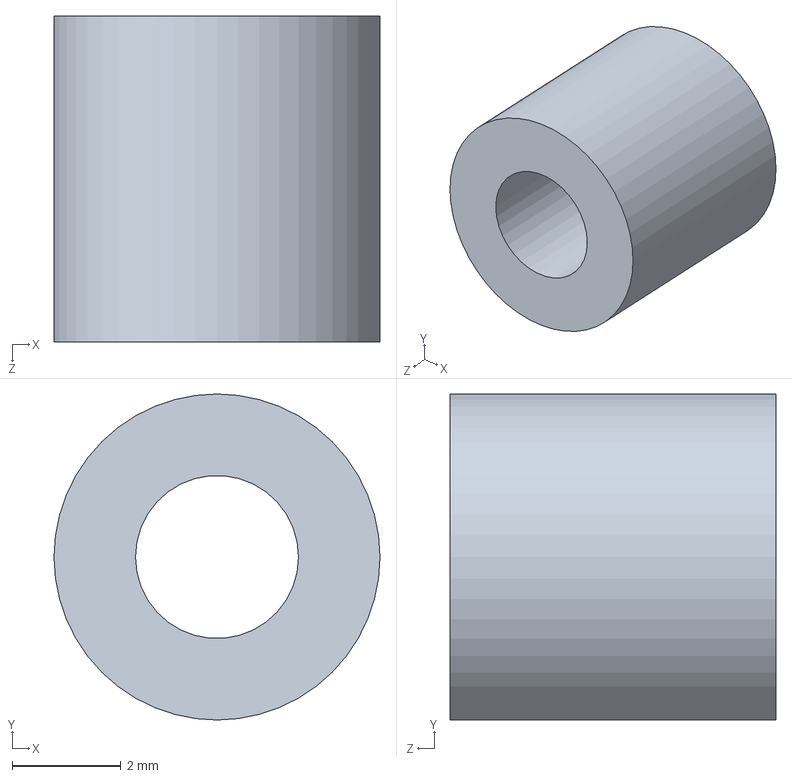
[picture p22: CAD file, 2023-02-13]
StudentSubmissions/elkedwanimiray/Micropump SolidWork Files/Micropump/Shrink Wrap.SLDPRT
6.00 x 6.00 x 6.00 mm

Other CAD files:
StudentSubmissions/elkedwanimiray/Micropump SolidWork Files/Micropump/Stepper Moter.SLDPRT
StudentSubmissions/elkedwanimiray/Micropump SolidWork Files/Micropump/New bearing.SLDPRT
Pump/535206.STEP
Pump/Bearing_hub_spring_new2.SLDPRT
Pump/Motor_enc_U.SLDPRT
Pump/Stl/Bearing_hub_spring_new.STL
Pump/Stl/Bearing_hub_spring_new2.STL
Pump/Stl/Motor_enc_U.STL
Pump/Stl/Pump_Assem.STL
StudentSubmissions/elkedwanimiray/Micropump SolidWork Files/Micropump/Bearing_hub_spring_new2.SLDPRT
StudentSubmissions/elkedwanimiray/Micropump SolidWork Files/Micropump/Final Assembly Draw.SLDDRW
StudentSubmissions/elkedwanimiray/Micropump SolidWork Files/Micropump/Large Washer.SLDPRT
StudentSubmissions/elkedwanimiray/Micropump SolidWork Files/Micropump/Mini Screw.SLDPRT
StudentSubmissions/elkedwanimiray/Micropump SolidWork Files/Micropump/Moter ECU Draw.SLDDRW
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

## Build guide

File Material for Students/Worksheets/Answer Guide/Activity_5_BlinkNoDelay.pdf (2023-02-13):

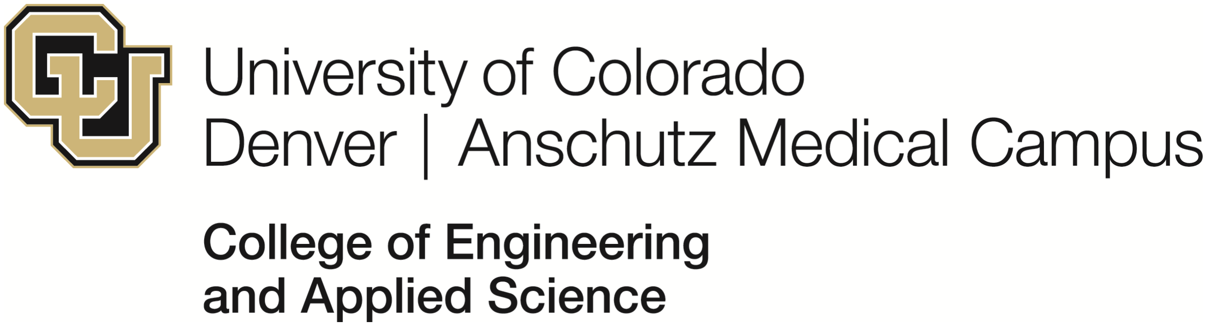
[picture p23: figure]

## Senior Design Bioe 4035

www.ucdenver.edu/Bioengineering │ bioengineeringinstructors@gmail.com

## Activity 5 – Blink No Delay

## To Do

£ Define Globals.
- currentTime
- lastTime
- switchTime
- ledState
- millis()
£ Create blink_timer() function.
£ Functionalize commands in loop
- Loop should now only consist of a single function named blink_timer()
- blink_led() will now be called from blink_timer()

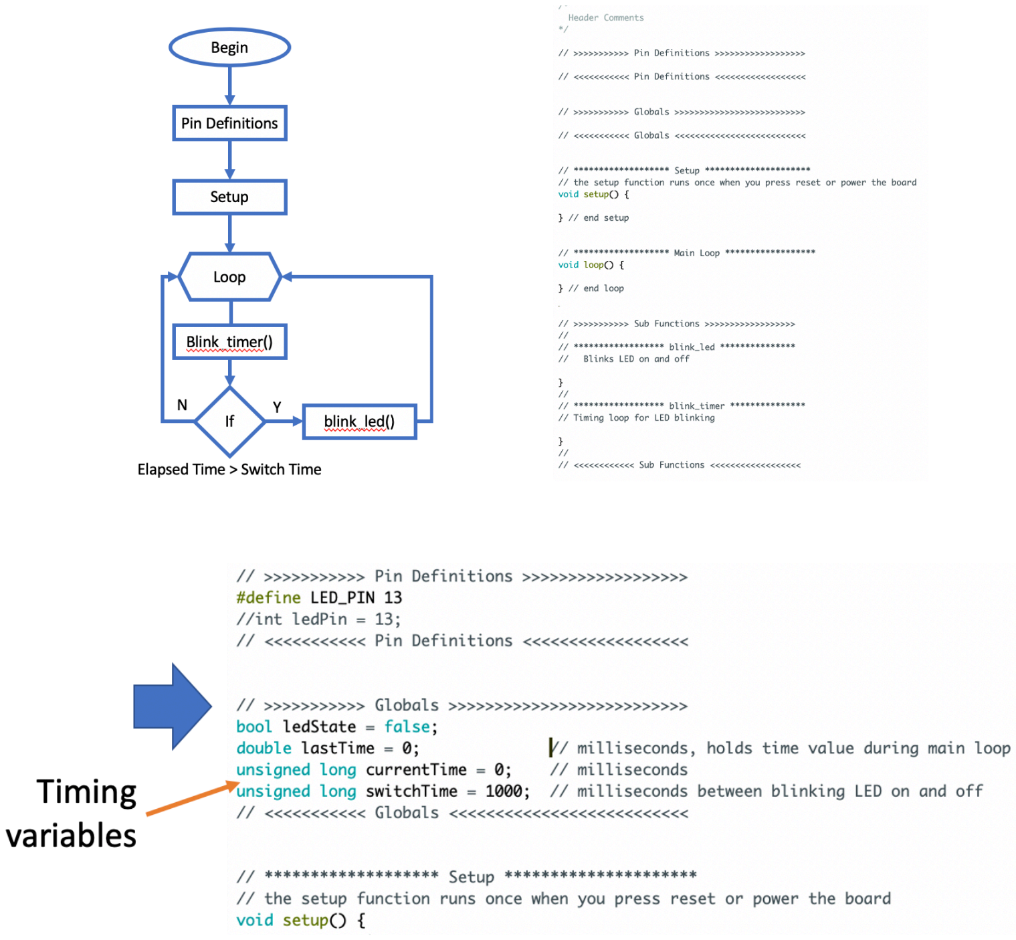
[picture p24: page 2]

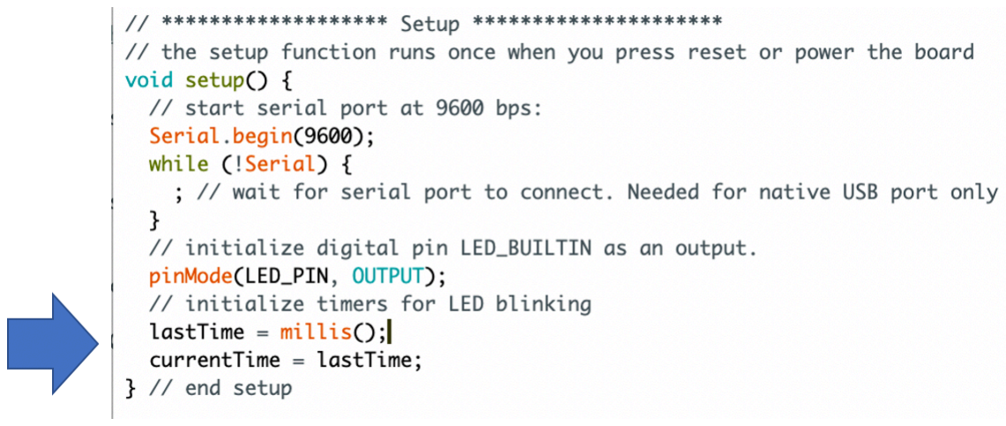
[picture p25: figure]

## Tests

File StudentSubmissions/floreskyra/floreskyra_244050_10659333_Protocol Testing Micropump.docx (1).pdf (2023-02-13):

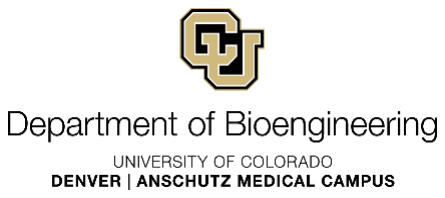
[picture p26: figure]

Intro. to Biodesign
BIOE 3090 | 3D Printing – Mechanical Testing Protocol

## Micropumps

### Mechanical Testing Protocol – 20 Pts

## ID: MTP-1

Due Date: 4/6/2020 11:59 PM, Canvas Upload

Testing Protocol: – (Micropump Testing MTP-1) Date Written – 4/4/2020
Date Revised – 4/6/2020
Author: Kyra Flores, Ana Meza, Uyen Nguyen, (https://ucdenver.instructure.com/courses/426016/users/217639) and Jonathan Tullos (https://ucdenver.instructure.com/courses/426016/users/223968)
Testing Protocol Description – (Peristaltic Micropump Testing Protocol)
This is the testing protocol for an Arduino controlled peristaltic micropump used to pump media through a bioreactor in an incubator. The Arduino will be taking in user inputs to calculate the motor speed. If there is no valid input, the motor will be set to default speed.
Tools and Equipment
# | Tool | Name / # if applicable | Location | Purpose

TE1 | Programming Software | Arduino | Computer file | An Arduino code that can takes in user interface to calculate motor speed and execute the pump
TE2 | Stepper Motor | NEMA 17 | GulfCoast Robotics (https://gulfcoast-robotics.com/products/nema-17-stepper-motor-57-oz-in-for-cnc-3d-printer-reprap-mendel-prusa-extruder-robot) | A motor used to rotate the pump
TE3 | Stepper Motor Driver | A4988 | GulfCoast Robotics (https://gulfcoast-robotics.com/products/a4988-stepper-motor-driver-module-3d-printer-polulu-stepstick-ramps-reprap-cnc) | Drive the stepper motor. Allow for control with simple directions and direction inputs.
TE4 | 12V Power Supply | inShareplus 12V LED Strip Power Supply | Amazon (https://www.amazon.com/inShareplus-Mounted-Switching-Connector-Adapter/dp/B01GD4ZQRS) | Provides enough power to drive the stepper motor to turn
TE5 | 220 μF Electrolytic Capacitor | | Guitar Pedal Parts (https://guitarpedalparts.com/products/220uf-electrolytic-capacitor?variant=18956414681188&currency=USD) | Stores electrical energy.

Intro. to Biodesign
BIOE 3090 | 3D Printing – Mechanical Testing Protocol

Materials
ID | Material | Purpose
MAT1 | 2-mm tubing | To connect to the system and allow for fluids to flow
MAT2 | Pushbutton | Start/stop the motor when pushed
MAT3 | LED | Indicate if the pump is turned on by flashing
MAT4 | PCB | Electrically connect components
MAT5 | Nuts, Bolts & Washers | To assemble the pump.

Machine Settings
# | Volumetric Flow Rate (mL/ms) | Tubing Diameter (cm) | Description

1 | 0.5 | 0.3 | Default setting
2 | 0.8 | 0.5 | Higher testing motor speed
3 | 0.3 | 0.3 | Slower testing motor speed

Values to be Recorded
| Values | Description
1 | Volumetric Flow Rate (mL/ms) | User input
2 | Tubing Diameter (cm) | User input
3 | Stepper Delay Value (sec/step) | Calculated value from the flow rate and tubing geometry that sets the speed for the motor

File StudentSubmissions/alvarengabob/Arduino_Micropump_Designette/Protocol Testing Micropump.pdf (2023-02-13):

Intro. to Biodesign
BIOE 3090 | Micropump – Mechanical Testing Protocol

## Micropump Module

### Micropump Testing Protocol – 15 Pts

## ID: MTD-1

Due Date: 04/06/2020 11:59 PM, Canvas Upload

Prototyping Protocol: – (Prototyping Protocol: PP-1) Date Written – 04/02/2020
Date Revised – 04/04/2020
Author: Alyssa Salazar, Bob Alvarenga, Gage Murray, Luis Rodriguez, Mikala Mueller Protocol Description – (Micropump Testing Protocol)
This protocol outlines the steps necessary to test the micropump along with the newly designed and printed PCB board shield. Following the successful assembly of the PCB board, attach it to the top of the Arduino. Assemble the pump and connect the pump to the PCB board. Once the assembly is complete, upload the finished Arduino code. Turn on the pump to make sure it is connected properly and functions correctly. Have a container of water nearby to test to see if the pump can transfer water. If successful, change the flow rate parameter of the motor through the user interface. Once changed, test to see if the motor spins faster/slower and water is transferred quicker/slower.
Tools and Equipment
ID | Tool | Name / # if applicable | Location | Purpose
TE1 | Computer | Mac Book | N/A | Design and create parts; Upload code to Arduino and change the pump flow rate
TE2 | PCB Circuit Software | Eagle | N/A | PCB board-specific software
TE3 | Soldering Kit | Elenco Deluxe | Design Lab | To solder required electronics of the circuit to the board
TE4 | Arduino Uno | Arduino Uno | Design Lab | To run the circuit
TE5 | Digital Multimeter | Digital Multimeter | Design Lab | To test if voltage is flowing through the components

TE6 Arduino IDE
Software
Software | Design Lab | Create code to test pump and user interface

Materials
ID | Material | Purpose
MAT1 | Fiberglass | Create PCB board
MAT2 | Epoxy Resin | Create PCB board
MAT3 | Copper foil/plate | Create PCB board
MAT4 | Wires | Circuit Assembly
MAT5 | Resistors | Circuit Assembly
MAT6 | Capacitor | Circuit Assembly
MAT7 | LED | Circuit Assembly
MAT8 | Button | Circuit Assembly
MAT9 | Stepper Motor Driver | Circuit Assembly
MAT10 | Stepper Motor | Pump Assembly
MAT11 | Pump Housing | Pump Assembly
MAT12 | Pump Rotor | Pump Assembly
MAT13 | Bearings | Pump Assembly
MAT14 | Screws | Pump Assembly
MAT15 | Nuts | Pump Assembly
MAT16 | Washers | Pump Assembly
MAT17 | Tubing | Pump Assembly

Compliance Testing
Testing PCB after printed to determine connection continuity using multimeter
ID | Board to Component | Pass/Fail
CT1 | LED | Pass
CT2 | Pump | Pass
CT3 | Arduino | Pass
CT4 | Button | Pass

To test the pump, add water to the tube and turn on the pump. If the pump properly extrudes the water, then it passes.
Pass or Fail:___________

Values to be Recorded
Test the pump at different speeds using the user interface. If the pump properly extrudes the water at different flow rates, then the pump passes
ID | Flow Rate (mL/s) | Pass or Fail
ST1 | 0.3 | Pass
ST2 | 0.6 | Pass
ST3 | 0.1 | Pass

Notes

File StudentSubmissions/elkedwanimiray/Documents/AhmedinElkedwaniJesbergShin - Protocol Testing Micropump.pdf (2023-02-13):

Intro. to Biodesign
BIOE 3090 | 3D Printing – Mechanical Testing Protocol

## Micropump Module

## Mechanical Testing Protocol

## ID: MTD-1

Due Date: 4/6/2020 11:59 PM, Canvas Upload

Mechanical Testing Protocol: – (PP-1)

Date Written – 4/1/2020

Date Revised – 4/6/2020

Author: Mewael Ahmedin, Miray Elkedwani, Parker Jesberg, Bo Shin

Protocol Description – (Mechanical Testing Protocol for PP-1)

With the upgrades that were added to the pump, as described in PP-1, the new design will be tested to verify it meets all the design verifications and validations. To test the new design flow rate, the flow rate of the old design will be timed and compared to that of the new design. The new design will have the same or faster flow rate as the old design.

The user interface will have the calculations needed to adjust the steps per second when the user inputs a flow rate and a tube diameter value. To test that the improved design will have the same or faster flow rate, a timer will be used to time how long it takes for a specific amount of water to get pumped through the micropump. This will then be compared to the old design; both designs should be around the same time.

To display the status of the motor, the LED light should turn green when the motor is turned on and will turn red when the motor is turned off. For all the other improvements, as stated in PP-1, they will be tested in a qualitative manner based on a pass or fail test. Overall, all testing will be defined by a pass or fail; this is done so that all the specifications are met for better user experience.

Tools and Equipment

# | Tool | Name / # if applicable | Location | Purpose

TE1 | Arduino Uno (Micropump circuit) | N/A | Design Lab | To read inputs and referenced in PP-1
TE2 | Timer | N/A | Design Lab | To time the flow rate of the new design and compare it to the old one
TE3 | 3D printed pump housing unit | N/A | Design Lab | Part of the pump design
TE4 | 3D printed pump rotor | N/A | Design Lab | Part of the pump design

Materials

ID | Material | Name / # if applicable | Location | Purpose
MAT1 | Water | N/A | N/A | For flow rate testing
MAT2 | Heat shrink tube | HS-615C | Online | To prevent the tube from slipping
MAT3 | Tygon tube | N/A | Design Lab | Part of the pump design

Improved Micropump Testing

ID | Test | Pass (Yes)/Fail (No)
IMT1 | Does the light turn red when the motor is off? | Pass (seen in the video)
IMT2 | Does the light turn green when the motor is on? | Pass (seen in the video)
IMT3 | Does the tube stay in place when the heat shrink tube is placed on it? | N/A
IMT4 | Does the new pumping design allow for easier insertion of the tubing? | N/A
IMT5 | Can the user easily enter different flow rates? | Pass (seen in the video)
IMT6 | Does the new design have the same or faster timing as the old design when set to the flow rate to pump water? | N/A

Values to be Recorded

ID | Design | Flow Rate (cm³ /min) | Time (sec)
VR1 | Old | Default = 1 | 25
VR2 | Improved | | N/A

Notes:

References for Materials

ID | Website Link
MAT2 | https://www.amazon.com/innhom-615pcs-Shrink-Tubing-Approved/dp/B07GS7PBHV (https://www.amazon.com/innhom-615pcs-Shrink-Tubing-Approved/dp/B07GS7PBHV)

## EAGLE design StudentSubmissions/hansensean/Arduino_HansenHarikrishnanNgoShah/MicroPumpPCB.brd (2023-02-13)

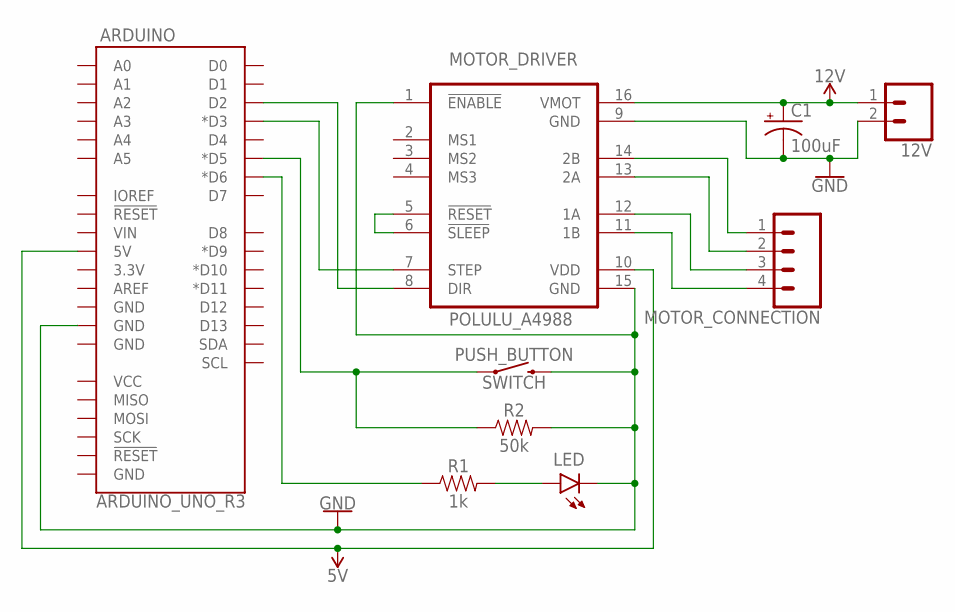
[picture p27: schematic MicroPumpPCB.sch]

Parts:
12V: CONN_02POLAR; MOLEX-1X2
ARDUINO: ARDUINO_UNO_R3; ARDUINO_R3
C1: 100uF; CPOL-RADIAL-2.5MM-6.5MM
LED: LED5MM; LED_5MM
MOTOR_CONNECTION: CONN_04; 1X04
POLULU_A4988: MOTOR_DRIVER; POLOLULU2128
PUSH_BUTTON: SWITCH; TACTILE_SWITCH_PTH_6.0MM
R1: 1k; AXIAL-0.3
R2: 50k; AXIAL-0.3

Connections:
5V: ARDUINO.5V, POLULU_A4988.10 (VDD)
12V: 12V.1, C1.1 (+), POLULU_A4988.16 (VMOT)
GND: 12V.2, ARDUINO.GND@3 (GND), C1.2 (-), LED.K (C), POLULU_A4988.1 (!ENABLE), POLULU_A4988.9 (GND), POLULU_A4988.15 (GND), PUSH_BUTTON.3 (2), R2.P$2 (2)
unnamed: ARDUINO.D2, POLULU_A4988.8 (DIR)
unnamed: ARDUINO.D3 (*D3), POLULU_A4988.7 (STEP)
unnamed: MOTOR_CONNECTION.1, POLULU_A4988.14 (2B)
unnamed: MOTOR_CONNECTION.2, POLULU_A4988.13 (2A)
unnamed: MOTOR_CONNECTION.3, POLULU_A4988.12 (1A)
unnamed: MOTOR_CONNECTION.4, POLULU_A4988.11 (1B)
unnamed: ARDUINO.D6 (*D6), R1.P$1 (1)
unnamed: LED.A, R1.P$2 (2)
unnamed: ARDUINO.D5 (*D5), PUSH_BUTTON.1, R2.P$1 (1)
unnamed: POLULU_A4988.5 (!RESET), POLULU_A4988.6 (!SLEEP)

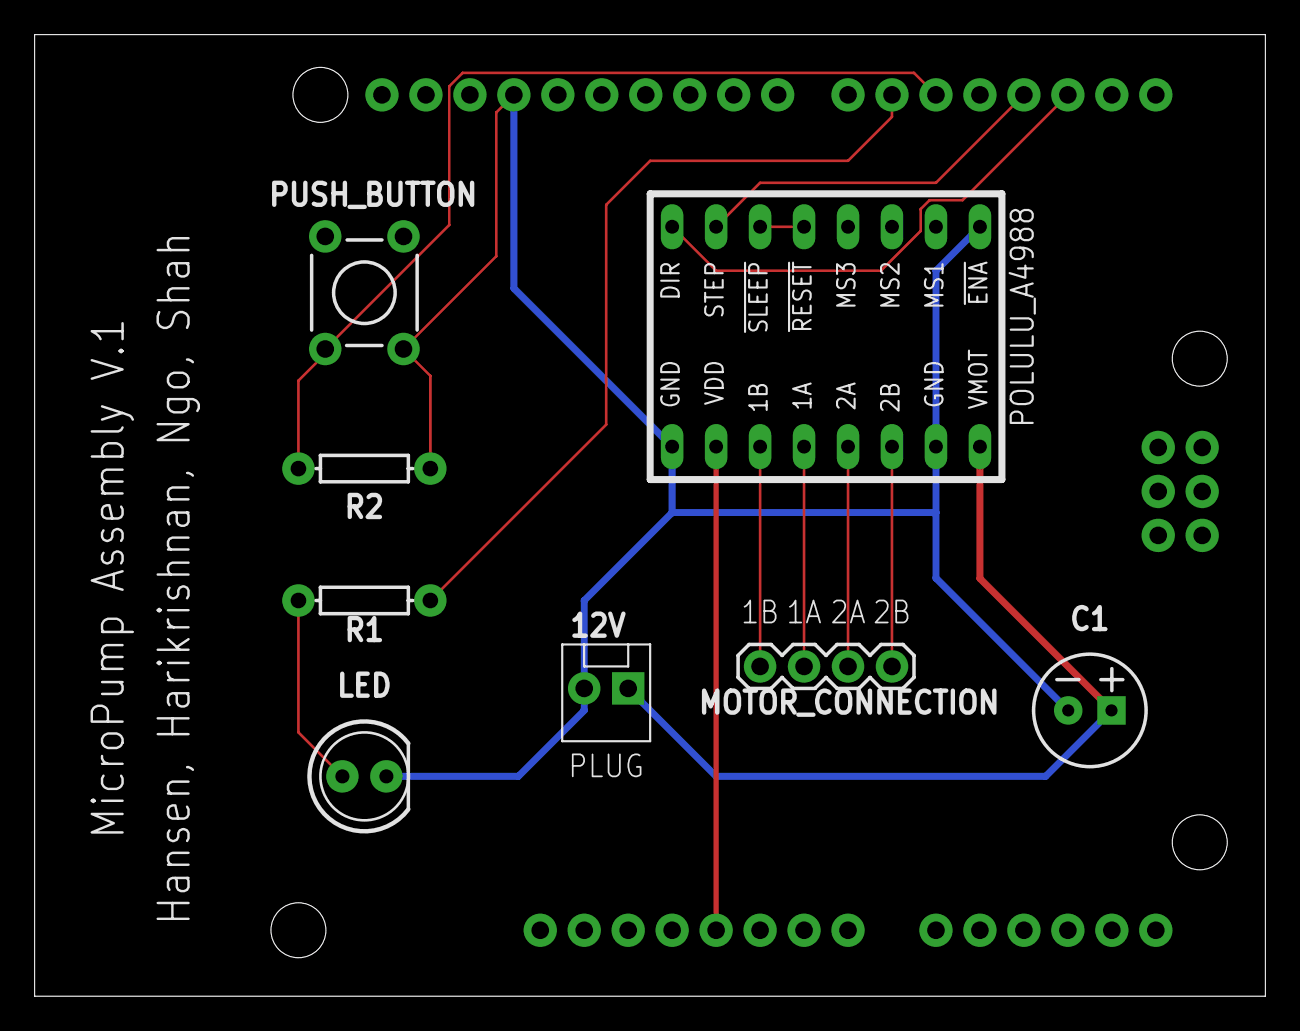
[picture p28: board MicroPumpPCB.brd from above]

Board: 2 copper layers, 71.1 x 55.5 mm, 9 parts (0 on the bottom side), 13 nets.

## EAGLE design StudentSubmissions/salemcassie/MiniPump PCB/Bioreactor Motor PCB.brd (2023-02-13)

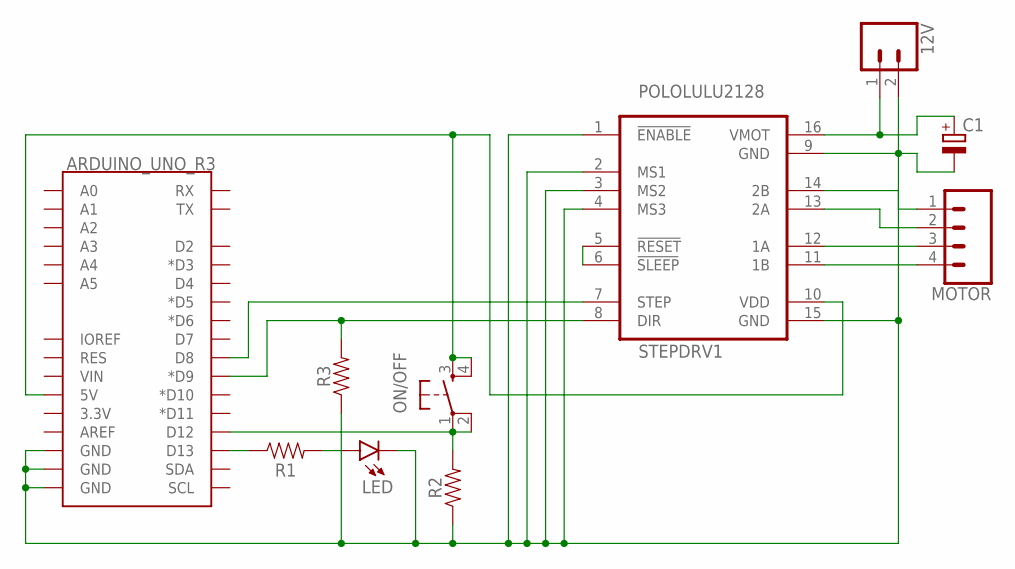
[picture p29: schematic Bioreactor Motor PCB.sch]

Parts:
12V: CONN_02POLAR; MOLEX-1X2
ARDUINO_UNO_R3: ARDUINO_UNO_R3_SHIELDBASIC; UNO_R3_SHIELD
C1: CPOL-EUE3.5-8; E3,5-8
LED: TLLG4400; LED3MM
MOTOR: CONN_04POLAR; MOLEX-1X4
ON/OFF: TAC_SWITCHPTH; TACTILE-PTH
R1: 1M; AXIAL-0.3
R2, R3: 1k; AXIAL-0.3
STEPDRV1: POLOLULU2128

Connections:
unnamed: 12V.2, ARDUINO_UNO_R3.GND@0 (GND), ARDUINO_UNO_R3.GND@1 (GND), ARDUINO_UNO_R3.GND@2 (GND), C1.-, LED.K (C), R2.P$1 (1), R3.P$1 (1), STEPDRV1.1 (!ENABLE), STEPDRV1.2 (MS1), STEPDRV1.3 (MS2), STEPDRV1.4 (MS3), STEPDRV1.9 (GND), STEPDRV1.15 (GND)
unnamed: ARDUINO_UNO_R3.D13, R1.P$1 (1)
unnamed: LED.A, R1.P$2 (2)
unnamed: ARDUINO_UNO_R3.D12, ON/OFF.1, ON/OFF.2, R2.P$2 (2)
unnamed: ARDUINO_UNO_R3.5V, ON/OFF.3, ON/OFF.4, STEPDRV1.10 (VDD)
unnamed: 12V.1, C1.+, STEPDRV1.16 (VMOT)
unnamed: STEPDRV1.5 (!RESET), STEPDRV1.6 (!SLEEP)
unnamed: ARDUINO_UNO_R3.D9 (*D9), R3.P$2 (2), STEPDRV1.8 (DIR)
unnamed: ARDUINO_UNO_R3.D8, STEPDRV1.7 (STEP)
unnamed: MOTOR.4, STEPDRV1.11 (1B)
unnamed: MOTOR.3, STEPDRV1.12 (1A)
unnamed: MOTOR.2, STEPDRV1.13 (2A)
unnamed: MOTOR.1, STEPDRV1.14 (2B)

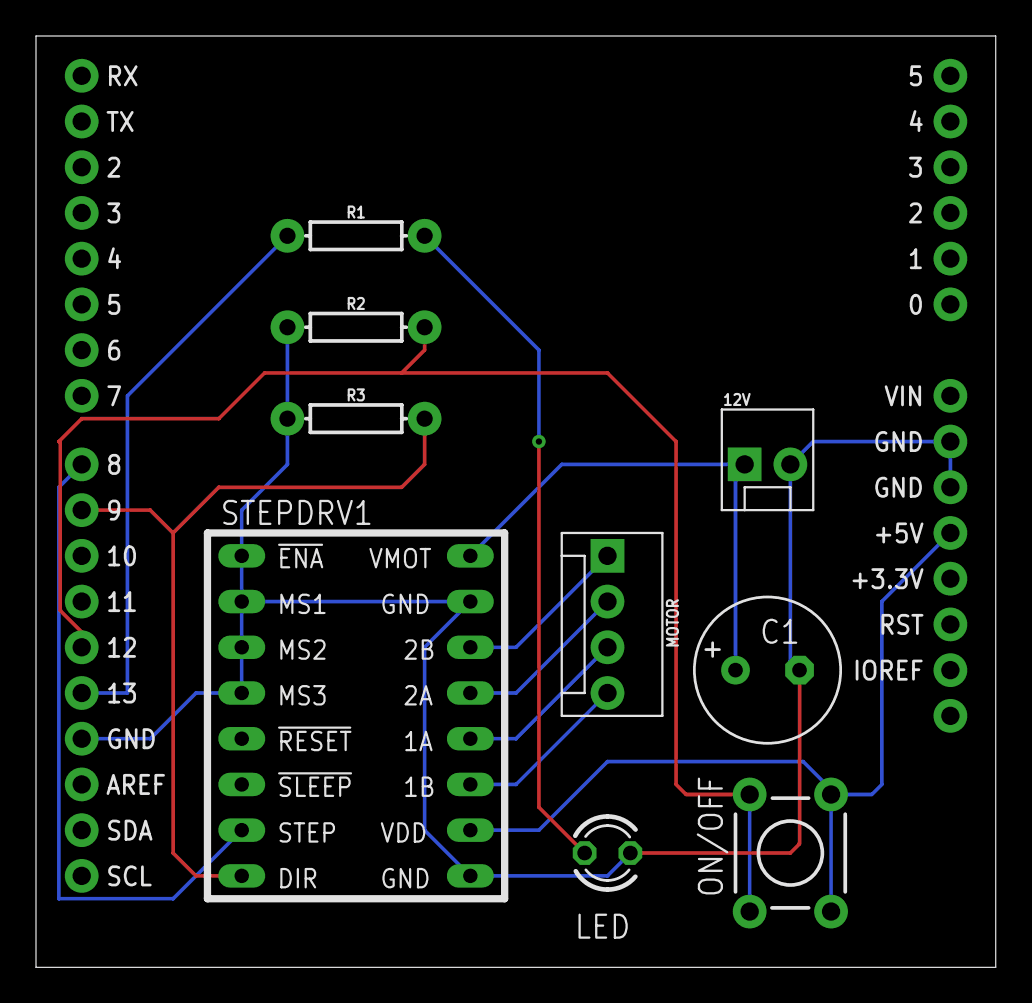
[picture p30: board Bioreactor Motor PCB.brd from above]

Board: 2 copper layers, 53.3 x 51.7 mm, 10 parts (0 on the bottom side), 13 nets.

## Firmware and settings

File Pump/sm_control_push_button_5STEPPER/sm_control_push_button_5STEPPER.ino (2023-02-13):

// DECLARE SWITCH CONTROL
int MOTORStateA = 0;
int buttonPINA = 52;
int buttonNewA;
int buttonOldA = 1;
//B
int MOTORStateB = 0;
int buttonPINB = 50;
int buttonNewB;
int buttonOldB = 1;
//C
int MOTORStateC = 0;
int buttonPINC = 48;
int buttonNewC;
int buttonOldC = 1;
//D
int MOTORStateD = 0;
int buttonPIND = 46;
int buttonNewD;
int buttonOldD = 1;
//E
int MOTORStateE = 0;
int buttonPINE = 44;
int buttonNewE;
int buttonOldE = 1;





// DECLARE MOTOR CONTROL
//A
const int stepsPerRev = 200; //         200/400 depending on stepper motor 
const int stepPinA = 3;
const int dirPinA = 2;
const int MS1A = 4 ;
const int MS2A = 5;
const int MS3A = 6;
//const int ENABLE = 13;

//B
const int stepPinB = 9;
const int dirPinB = 8;
const int MS1B = 10 ;
const int MS2B = 11;
const int MS3B = 12;

//C
const int stepPinC = 23;
const int dirPinC = 22;
const int MS1C = 24 ;
const int MS2C = 25;
const int MS3C = 26;


//D
const int stepPinD = 28;
const int dirPinD = 27;
const int MS1D = 29 ;
const int MS2D = 30;
const int MS3D = 31;

//E
const int stepPinE = 34;
const int dirPinE = 33;
const int MS1E = 35 ;
const int MS2E = 36;
const int MS3E = 37;

void setup() {
Serial.begin(9600); 
pinMode(buttonPINA, INPUT);

   //Declare pins as outputs
pinMode(dirPinA,OUTPUT);
pinMode(stepPinA,OUTPUT);
pinMode(MS1A,OUTPUT);
pinMode(MS2A,OUTPUT);
pinMode(MS3A,OUTPUT);
//pinMode(13,OUTPUT);
//B
pinMode(dirPinB,OUTPUT);
pinMode(stepPinB,OUTPUT);
pinMode(MS1B,OUTPUT);
pinMode(MS2B,OUTPUT);
pinMode(MS3B,OUTPUT);
//C
pinMode(dirPinC,OUTPUT);
pinMode(stepPinC,OUTPUT);
pinMode(MS1C,OUTPUT);
pinMode(MS2C,OUTPUT);
pinMode(MS3C,OUTPUT);
//D
pinMode(dirPinD,OUTPUT);
pinMode(stepPinD,OUTPUT);
pinMode(MS1D,OUTPUT);
pinMode(MS2D,OUTPUT);
pinMode(MS3D,OUTPUT);
//E
pinMode(dirPinE,OUTPUT);
pinMode(stepPinE,OUTPUT);
pinMode(MS1E,OUTPUT);
pinMode(MS2E,OUTPUT);
pinMode(MS3E,OUTPUT);

  //set direction, ENABLE set to LOW--FET OUTPUTS controlled by controller
  digitalWrite(dirPinA, HIGH);  
  //digitalWrite(13, LOW);
  digitalWrite(dirPinB, HIGH);
  digitalWrite(dirPinC, HIGH);
  digitalWrite(dirPinD, HIGH);
  digitalWrite(dirPinE, HIGH);
  
  //sets microstepping resolution to eigth step (see microstepping resolution truth table for A4988 stepper motor controller)
  digitalWrite(MS1A, HIGH);
  digitalWrite(MS2A, HIGH);
  digitalWrite(MS3A, HIGH);
  //B
  digitalWrite(MS1B, HIGH);
  digitalWrite(MS2B, HIGH);
  digitalWrite(MS3B, HIGH);
  //C
  digitalWrite(MS1C, HIGH);
  digitalWrite(MS2C, HIGH);
  digitalWrite(MS3C, HIGH);
  //D
  digitalWrite(MS1D, HIGH);
  digitalWrite(MS2D, HIGH);
  digitalWrite(MS3D, HIGH);
  //E
  digitalWrite(MS1E, HIGH);
  digitalWrite(MS2E, HIGH);
  digitalWrite(MS3E, HIGH);

  //for (int x = 0 ; x < stepsPerRev; x++) {
  //  digitalWrite(stepPin,HIGH);
  //  delay(1);
  //  digitalWrite(stepPin,LOW);
  //  delay(1);
  //}


}

void loop() {

//  
  digitalWrite(stepPinA, HIGH);
  delay(5); // 200/400 steps per rev stepper motor, 4000 microseconds * 2 (low+high) per step
  digitalWrite(stepPinA, LOW);
  delay(5);
  buttonNewA=digitalRead(buttonPINA);

  if(buttonOldA==0 && buttonNewA==1){
    if(MOTORStateA==0){
      pinMode(dirPinA, INPUT);
      pinMode(stepPinA, INPUT);
     
      MOTORStateA=1;
      } 
     else{
      pinMode(dirPinA, OUTPUT);
      pinMode(stepPinA, OUTPUT);
     
      MOTORStateA = 0;
     } 
       
  }

  //  B
  digitalWrite(stepPinB, HIGH);
  delay(5); // 200/400 steps per rev stepper motor, 4000 microseconds * 2 (low+high) per step
  digitalWrite(stepPinB, LOW);
  delay(5);
  buttonNewB=digitalRead(buttonPINB);

  if(buttonOldB==0 && buttonNewB==1){
    if(MOTORStateA==0){
      pinMode(dirPinB, INPUT);
      pinMode(stepPinB, INPUT);
     
      MOTORStateB=1;
      } 
     else{
      pinMode(dirPinB, OUTPUT);
      pinMode(stepPinB, OUTPUT);
     
      MOTORStateA = 0;
     } 
       
  }

  //  C
  digitalWrite(stepPinC, HIGH);
  delay(5); // 200/400 steps per rev stepper motor, 4000 microseconds * 2 (low+high) per step
  digitalWrite(stepPinC, LOW);
  delay(5);
  buttonNewC=digitalRead(buttonPINC);

  if(buttonOldC==0 && buttonNewC==1){
    if(MOTORStateC==0){
      pinMode(dirPinC, INPUT);
      pinMode(stepPinC, INPUT);
     
      MOTORStateC=1;
      } 
     else{
      pinMode(dirPinC, OUTPUT);
      pinMode(stepPinC, OUTPUT);
     
      MOTORStateC = 0;
     } 
       
  }

  //  
  digitalWrite(stepPinD, HIGH);
  delay(5); // 200/400 steps per rev stepper motor, 4000 microseconds * 2 (low+high) per step
  digitalWrite(stepPinD, LOW);
  delay(5);
  buttonNewD=digitalRead(buttonPIND);

  if(buttonOldD==0 && buttonNewD==1){
    if(MOTORStateD==0){
      pinMode(dirPinD, INPUT);
      pinMode(stepPinD, INPUT);
     
      MOTORStateD=1;
      } 
     else{
      pinMode(dirPinD, OUTPUT);
      pinMode(stepPinD, OUTPUT);
     
      MOTORStateD = 0;
     } 
       
  }

  //  E
  digitalWrite(stepPinE, HIGH);
  delay(5); // 200/400 steps per rev stepper motor, 4000 microseconds * 2 (low+high) per step
  digitalWrite(stepPinE, LOW);
  delay(5);
  buttonNewE=digitalRead(buttonPINE);

  if(buttonOldE==0 && buttonNewE==1){
    if(MOTORStateE==0){
      pinMode(dirPinE, INPUT);
      pinMode(stepPinE, INPUT);
     
      MOTORStateE=1;
      } 
     else{
      pinMode(dirPinE, OUTPUT);
      pinMode(stepPinE, OUTPUT);
     
      MOTORStateE = 0;
     } 
       
  }

     buttonOldA = buttonNewA;
     buttonOldB = buttonNewB;
     buttonOldC = buttonNewC;
     buttonOldD = buttonNewD;
     buttonOldE = buttonNewE;
        
  // put your main code here, to run repeatedly:

  //for(int x = 0; x < stepsPerRev; x++)
  //{
//
//  digitalWrite(stepPin, HIGH);
//  delay(5); // 200/400 steps per rev stepper motor, 4000 microseconds * 2 (low+high) per step
//  digitalWrite(stepPin, LOW);
//  delay(5);


  //}
  //delayMicroseconds(2000);
}

// Define pin connections & motor's steps per revolution
//const int dirPin = 3;
//const int stepPin = 4;
//const int stepsPerRevolution = 200;
//
//void setup()
//{
//  // Declare pins as Outputs
//  pinMode(stepPin, OUTPUT);
//  pinMode(dirPin, OUTPUT);
//}
//void loop()
//{
//  // Set motor direction clockwise
//  digitalWrite(dirPin, HIGH);
//
//  // Spin motor slowly
//  for(int x = 0; x < stepsPerRevolution; x++)
//  {
//    digitalWrite(stepPin, HIGH);
//    delayMicroseconds(2000);
//    digitalWrite(stepPin, LOW);
//    delayMicroseconds(2000);
//  }
//  delay(1000); // Wait a second
//
//  // Set motor direction counterclockwise
//  digitalWrite(dirPin, LOW);
//
//  // Spin motor quickly
//  for(int x = 0; x < stepsPerRevolution; x++)
//  {
//    digitalWrite(stepPin, HIGH);
//    delayMicroseconds(1000);
//    digitalWrite(stepPin, LOW);
//    delayMicroseconds(1000);
//  }
//  delay(1000); // Wait a second
//}

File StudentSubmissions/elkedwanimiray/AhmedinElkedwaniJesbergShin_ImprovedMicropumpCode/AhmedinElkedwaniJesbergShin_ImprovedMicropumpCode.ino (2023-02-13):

/*
  This code controls the micropump with a pushbutton. As the pushbutton is pressed
  the motor will start rotating and the LED will start blinking, and when the button 
  is pressed again, the motor will stop and the LED will turn off. Moreover, the user
  can input different flow rates and tube diameters and the steps of the motor will be
  adjusted accordingly.To improve the user experience we added a tri color LED that turns
  red when the motor in turned off and green when it is on. 

  Turns an LED on for one second, then off for one second, repeatedly.

  Pin 13 – Digital out: LED

  created 25 Feburary 2020
  by Steve Lammers
  Updated: 6 April 2020
  by Miray Elkedwani
  
  This example code is in the public domain.

  Source code adapted from - http://www.arduino.cc/en/Tutorial/Blink
*/

// >>>>>>>>>>> Pin Definitions >>>>>>>>>>>>>>>>>>
#define RED_PIN 5        //Red LED control
#define GREEN_PIN 6        //Green LED control
#define BLUE_PIN 7        //Blue LED control   
#define PB_PIN 12         //Pushbutton
#define STEP_PIN 8        //Stepper driver steps once on low to high transition
#define DIR_PIN 9         // Sets stepper motor direction on stepper driver
#define pi 3.14159265359  // setting pi value for calculations
// <<<<<<<<<<< Pin Definitions <<<<<<<<<<<<<<<<<<


// >>>>>>>>>>> Globals >>>>>>>>>>>>>>>>>>>>>>>>>>
bool ledState = false;                  // Boolean latch for LED status
bool pbLatch = false;                   // Boolean latch for controlling LED blink
bool UserInputs = false;                // Boolean latch asl=king for user inputs
bool MotorState = true;                 // Boolean latch for stepper motor status
double lastTime = 0;                    // milliseconds, holds time value during main loop
double lastTimeMotor = 0;               // milliseconds, holds last time for motor
double FlowRate;                        // User input for flow rate
double TubeDiameter;                    // User input for tube diameter
double AngularVelocity;                // Angular Velocity for pump (calculation)
unsigned long currentTime = 0;          // milliseconds 
unsigned long switchTime = 1000;        // milliseconds between blinking LED on and off
unsigned long stepperDelay = 5;    // milliseconds between stepper motor steps
unsigned long pbLastDebounceTime = 0;   // milliseconds time of last pb press
unsigned long pbDebounceDelay = 50;     // milliseconds delay for pushbutton
//int stepperDelay=5;                     // milliseconds between motor steps
// <<<<<<<<<<< Globals <<<<<<<<<<<<<<<<<<<<<<<<<<


// ******************* Setup *********************
// the setup function runs once when you press reset or power the board
void setup() {
  // start serial port at 9600 bps:
  Serial.begin(9600);
  while (!Serial) {
    ; // wait for serial port to connect. Needed for native USB port only
  }
  // initialize digital the LEDS as an inputs and pushbutton as output.
  pinMode(RED_PIN, OUTPUT);
  pinMode(GREEN_PIN, OUTPUT);
  pinMode(BLUE_PIN, OUTPUT);
  pinMode(PB_PIN, INPUT);
  
  // initialize timers for LED blinking
  lastTime = millis();
  currentTime = lastTime;
  stepper_forward();
} // end setup


// ******************* Main Loop ******************
void loop() {

  //The micropump won't work and will go directly to user inputs
  if (UserInputs == false){
  user_inputs();
}
  // Check Pushbutton State
  // and toggle pbLatch
  pbLatch=check_pushbutton(pbLatch);

  // Run stepper motor if PB is latched on
  run_stepper(pbLatch);
  
} // end loop


// >>>>>>>>>>> Sub Functions >>>>>>>>>>>>>>>>>>
//
//
// ****************** Green and red LED colors ***************
//   LED will turn red when the motor is off and green when the button 
//   is pushed and the motor is rotating
//   
bool check_pushbutton(bool latchValue) { // check push button & toggle pbLatch
  
 if (digitalRead(PB_PIN)){ // Poll state of the pushbutton, debounce if siganl is there
  latchValue = pb_debounce(latchValue); 
    while(digitalRead(PB_PIN)){  
    }
 }
// Turns the LED red if latchValue is false 
 if (latchValue == false){ 
  digitalWrite(RED_PIN, HIGH);
   digitalWrite(GREEN_PIN, LOW);
   digitalWrite(BLUE_PIN, LOW);
 }
// Serial.println(latchValue);
 return latchValue;
}

//

// Turns green LED on when the button is pushed
bool pb_debounce(bool latchValue) {
  pbLastDebounceTime = millis();
  delay(pbDebounceDelay);
  if(digitalRead(PB_PIN)) {
    latchValue = !latchValue;
    digitalWrite(GREEN_PIN, HIGH);
   digitalWrite(RED_PIN, LOW);
   digitalWrite(BLUE_PIN, LOW);
  }
  return latchValue;
}

// ****************** stepper_forward ***************
// Stepper motor step controls
//
void stepper_forward(void){
  digitalWrite(DIR_PIN, HIGH);
}
//
//   
// ****************** stepper_backward ***************
// Stepper motor step controls
void stepper_backward(void){
  digitalWrite(DIR_PIN, LOW);
}
//   
// ****************** run_stepper ***************
// Stepper motor step controls
//
void run_stepper(bool latchValue){
  //Run stepper if pushbutton is latched
  // latchValue is pushbutton state
  if (latchValue){
    digitalWrite(STEP_PIN, HIGH);
    delay(stepperDelay);
    digitalWrite(STEP_PIN, LOW);
    delay(stepperDelay);
  }
}
//
//
// ****************** user_inputs ***************
// Ask user to input flow rate and tube diameter and it automatically adjusts the angular velocity
void user_inputs(){
  Serial.println("Please input flowrate (in cm^3/min) and tube diameter (in cm)");
  Serial.print("Volumetric Flowrate = ");
  while(!Serial.available()) {} //waits for user input
  if(Serial.available() > 0){ //gets an input from the user
     FlowRate = (Serial.parseFloat()); //set variables to floats
     Serial.print(FlowRate); //print flowrate value to serial monitor
     Serial.println (" cm^3/min ");  
     FlowRate = FlowRate/60; //setting flowrate (in seconds)
     Serial.read(); // throw the rest of the buffer
  }
  Serial.print("Tubing Diameter = ");
  while(!Serial.available()) {} //waits for user input
  if(Serial.available() > 0){ //gets an input from the user
     TubeDiameter = Serial.parseFloat(); //set variables to floats
     Serial.print(TubeDiameter); //print tube diameter value to serial monitor
     Serial.println (" cm "); 
}

//Setting Defults if user didn't put any input
//if the user didn't input any value for flow rate it will automatically go to the default
if(FlowRate == 0){
  FlowRate = 1;
  Serial.println("No input for flow rate, setting to default = 1 cm^3/min");
  FlowRate = FlowRate/60; //seting flow rate to 1 cm^3/min (in seconds) 
}
//if the user didn't input any value for the tube diameter it will automatically go to the default
if(TubeDiameter == 0){
  Serial.println("No input for tube diameter, setting to default = 0.2 cm");
  TubeDiameter = 0.2; //setting tube diameter to 0.2 cm (given tube size)
}
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

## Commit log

2020-02-25 pump added
    [Bearing_hub_spring_new.SLDPRT, Motor_enc_U.SLDPRT, Parts_List.xlsx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]
2023-02-13 general updates
    [535206.STEP, Bearing Carrier Assem.SLDASM, Bearing_535206.SLDPRT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]

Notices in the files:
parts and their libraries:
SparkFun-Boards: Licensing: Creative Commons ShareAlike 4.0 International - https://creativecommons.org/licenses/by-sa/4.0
